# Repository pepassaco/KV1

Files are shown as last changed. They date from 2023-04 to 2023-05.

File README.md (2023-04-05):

# KV1: A hydrofoil-based flying kayak 

**IMPORTANT**: This project is currently UNDER DEVELOPMENT and in the prototyping stage. As a result, the final deisgn has not been tested yet. Build it at your own risk. Any kind of advice, testing or collaboration will be highly appreciated :)

## Recommended guides and related projects

First things first. 

- Optimal Cl/Cd ratio: [video](https://www.youtube.com/watch?v=RyCcKV8puSE)
- Calculating lift in hydrofoils: [Forum discussion](https://www.boatdesign.net/threads/calculating-lift-bernoulli-forces-on-hydrofoil-for-windsurfing-board.60062/)
- List of tutorials on how to design and simulate an airfoil(/hydrofoil) in XFLR 5 from zero (in Spanish): [link 1](https://www.youtube.com/watch?v=bGubYDDyFB4), [link 2](https://www.youtube.com/watch?v=IUO3XJQxrvs), [link 3](https://www.youtube.com/watch?v=fuJba9P9ncE), [link 4](https://www.youtube.com/watch?v=owMY_eJGt3o)
- What we want to achieve: [video 1](https://www.youtube.com/watch?v=-VyOZVtOWoI)

## Design considerations

The design stage of this project took place under the following constraints:

- At cruising speed, no part of the hull must be touching the water
- The foils must be able to lift a person with a body mass of at least 90Kg
- The hydrodynamic lift must be greater than the weight of the paddler and the vessel for velocities as low as 3.5m/s
- All of the above must take place in fresh calm water at at least 15ºC

While due to their fluid-mechanical nature these are the main considerations to have into account in this stage, there are other important conditions for this project to succeed, such as the hydrofoils being relatively lightweight and resilient or being able to manufacture with enough accuracy.

## Obtaining the right airfoil shape

The very first step in this case is analysing our fluid so that we can adequately choose the optimal hydrodynamic foil shape. Assuming an average salinity of our water of 10g/Kg, at 15ºC, its kinematic viscosity will be of about 1,15e6 m^2/s: 

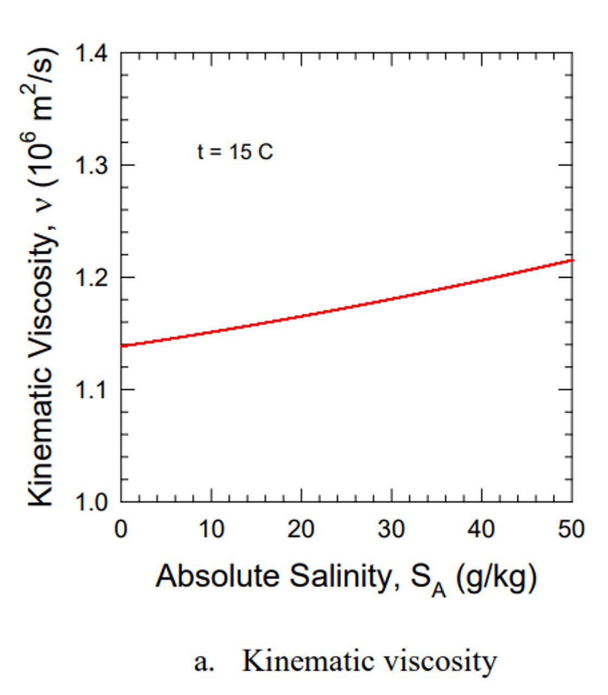
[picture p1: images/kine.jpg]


Pluggin this value in the definition of Reynold's NUmber, we get Re ~ 5.2e5:

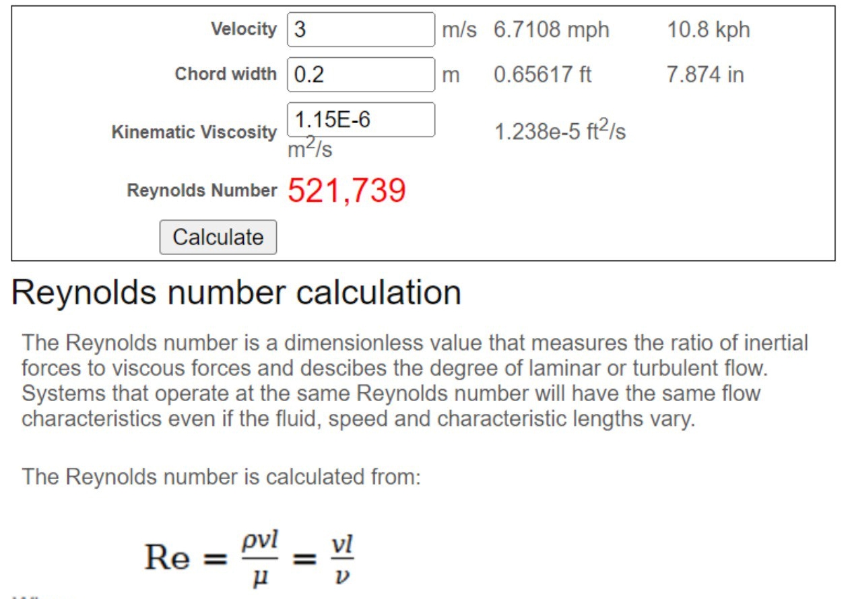
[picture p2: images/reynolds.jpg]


Taking this value into account, it was determined that an airfoil [NACA 4412](http://airfoiltools.com/airfoil/details?airfoil=naca4412-il) resulted in one of the best candidates to be used in this project, due to both its high lift coefficient (Cl) as well as lift-drag tadio (Cl/Cd) at low Angles of Attack:

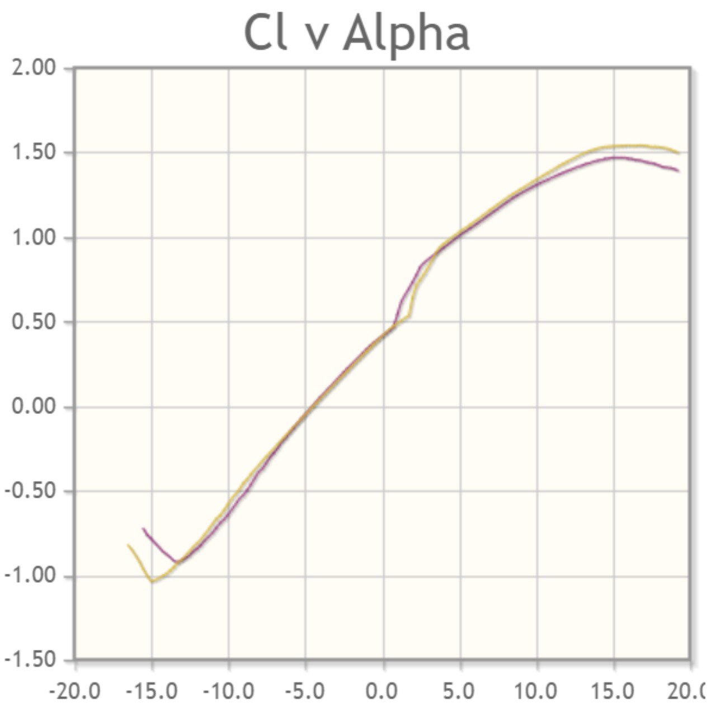
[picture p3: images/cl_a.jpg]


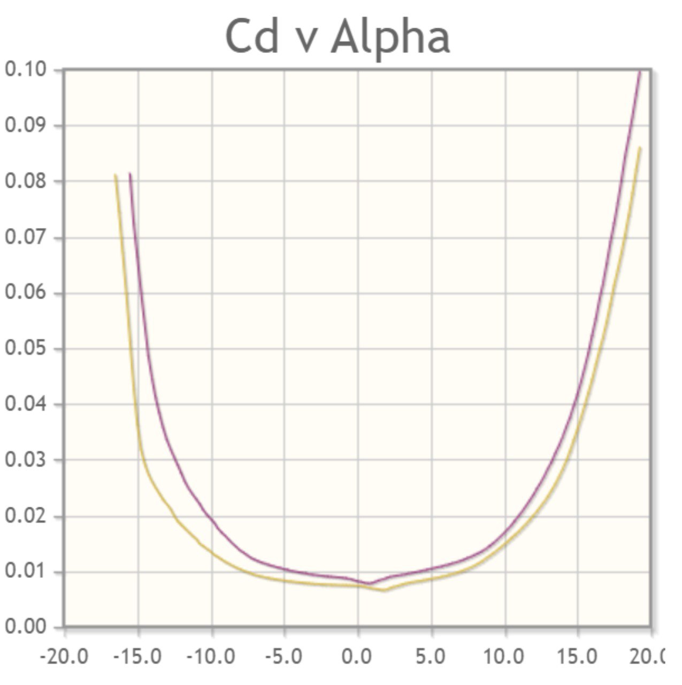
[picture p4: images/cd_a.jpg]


Moreover, it was decided that at cruising speed, the AoA of the main foil should be of 5º in order to maximize Cl/Cd. 

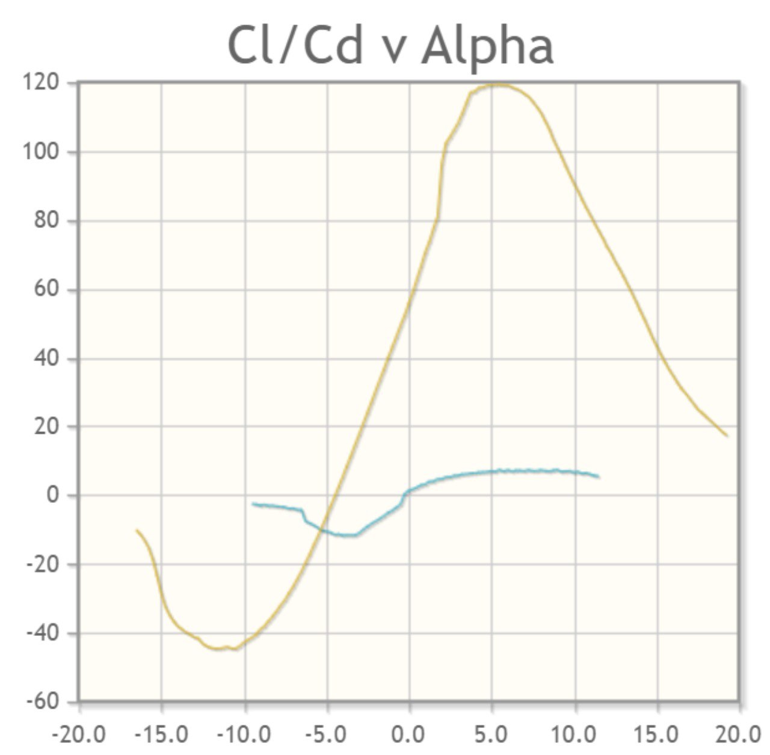
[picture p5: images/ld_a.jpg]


Note however that in the transition phase from water to air, we expect the front hydrofoil to lift first, inducing an extra AoA in the main wing. Taking into accoun the geometry of a K1 (5,4m of length), this increase in the AoA can be obtained in an approximate way (it will depend on the final position in the Z axis of the foils) achieving values from 5º to 8º, leading to global AoAs of between 10º and 13º. As we can see in the plot of Cl vs AoA, these are exactly the angles that maximize lift, helping pushing the paddler upwards.

## Computing the shape and angles of the hydrofoils

The shape and angles of the hydrofoils were obtained by means of the numerical simulation software [XFLR5](https://sourceforge.net/projects/xflr5/files/). First, an approximation for the global size of the airfoils was determined in terms of the lift force we require. Then, their aspect ratios were chosen so that they are the largest possible (for minimising drag) without impacting the maneuverability of the vessel (excessively long hydrofoils can be unconfortable for paddling) and manufacturing requirements (in our particular case, the longest piece must be less than 1m long). Finally, it was time to tweek the remaining parameters: the exact position of the hydrofoils in the X axis of the vessel with respect to the center of mass, their depth or position in the Z axis, the AoA of the front foil and the shape and width of the masts that will attach the foils to the hull.

The optimization of these parameters was carried out by finding a slightly positive Momentum Coefficient (Cm) at 0º of vessel pitching that becomes 0 for low pitching angles (around 2º in this case). The physical meaning of this is that, when reaching certain threshold speed (the rotation speed) with the kayak perfectly flat, the lift generated will be enought for both lifting the bow, generating pitching in the vessel and increasing the AoA. At 2º of pitching, Cm will equal 0, so it should remain in that orientation indefinitely:

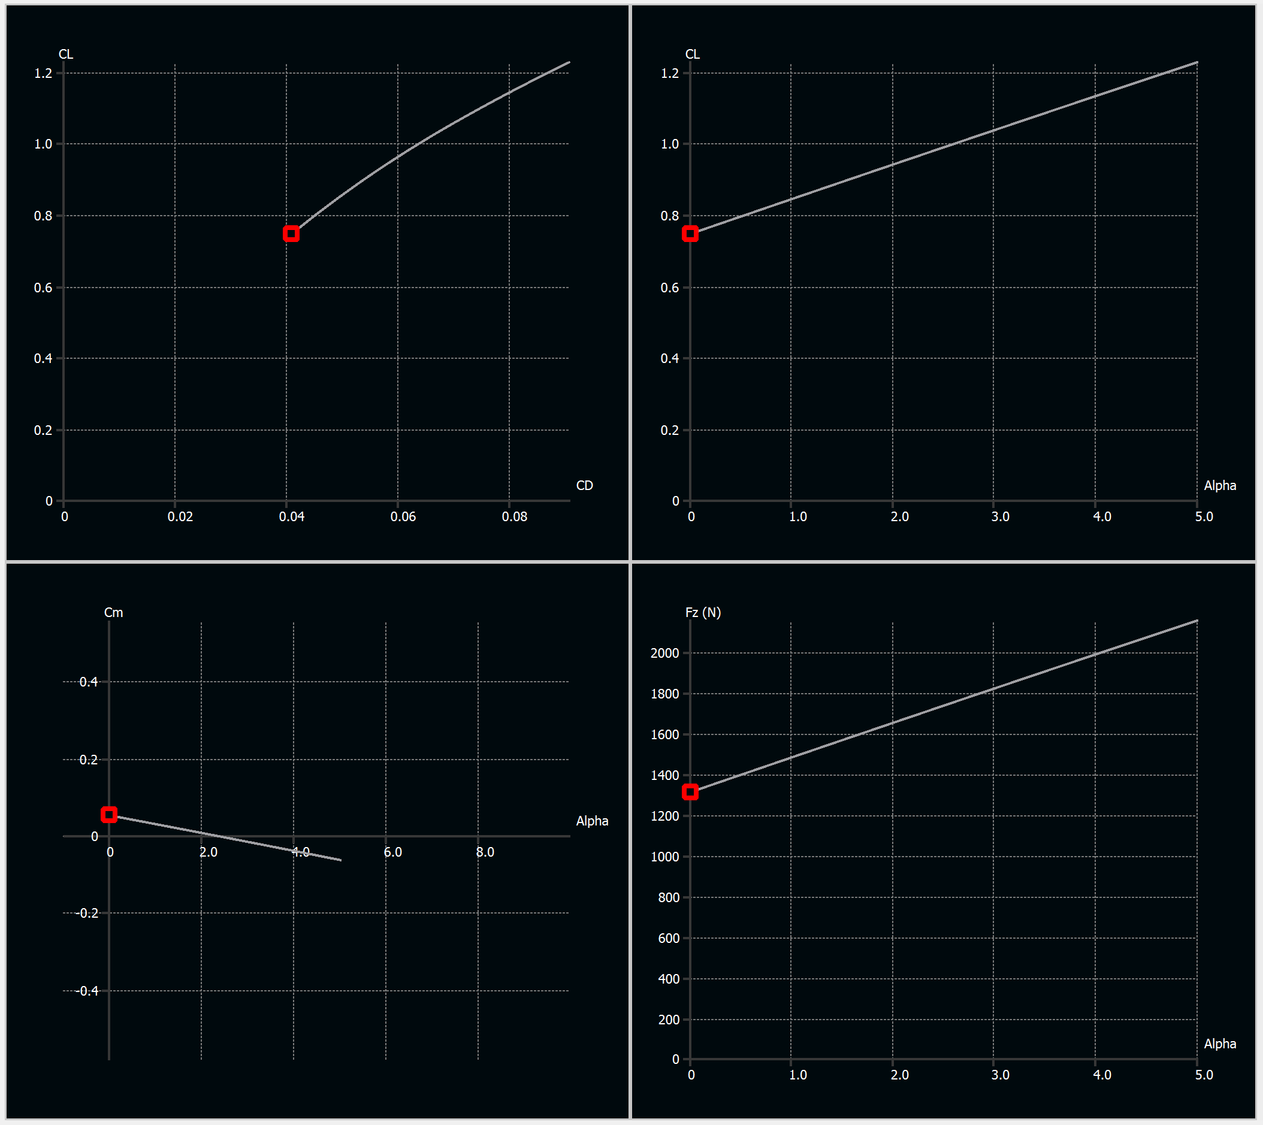
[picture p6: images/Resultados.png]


Note that, in the lower-right plot, we can see the lift force caused by both hydrofoils. It is always greater than 1200N, so that, even assuming a relatively large security margin, the lift forces will cancel out (and even be greater than) the weigth forces, so the vessel will start "flying".

The final deign can be seen in the following images (the XFLR5 file is also included in the folder simulations/):

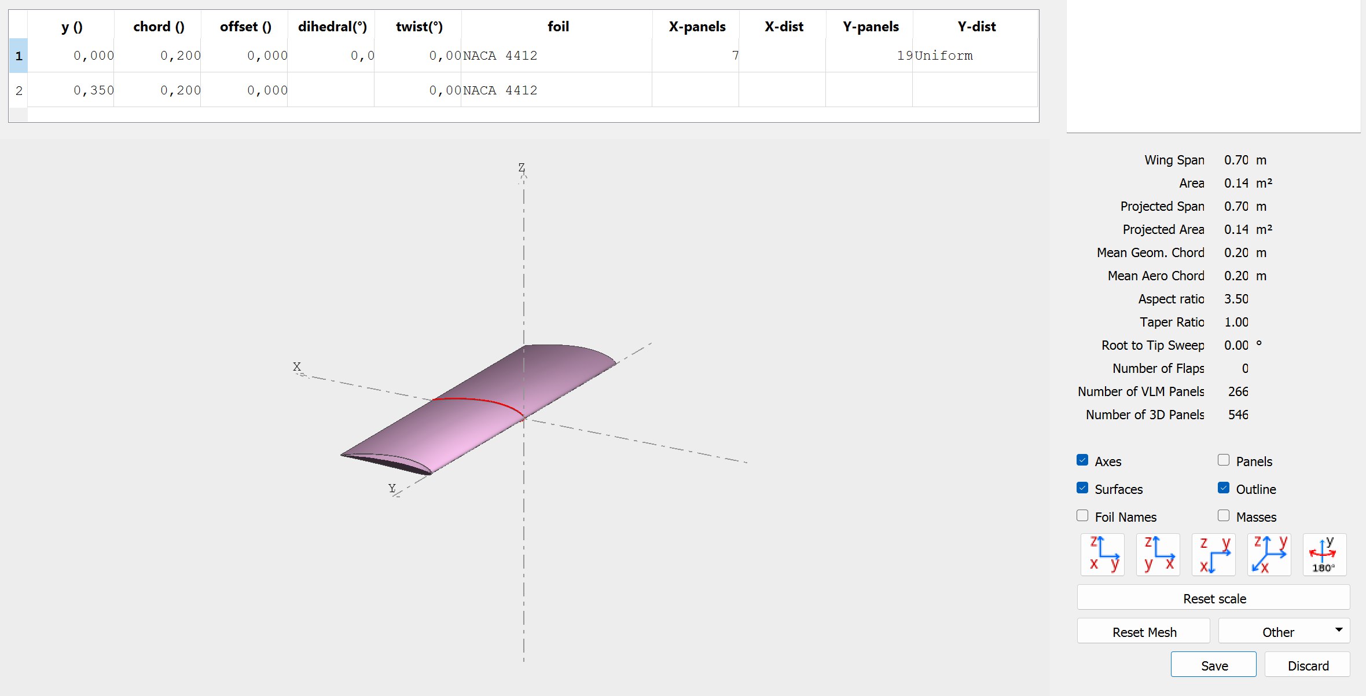
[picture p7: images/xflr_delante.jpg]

Front hydrofoil

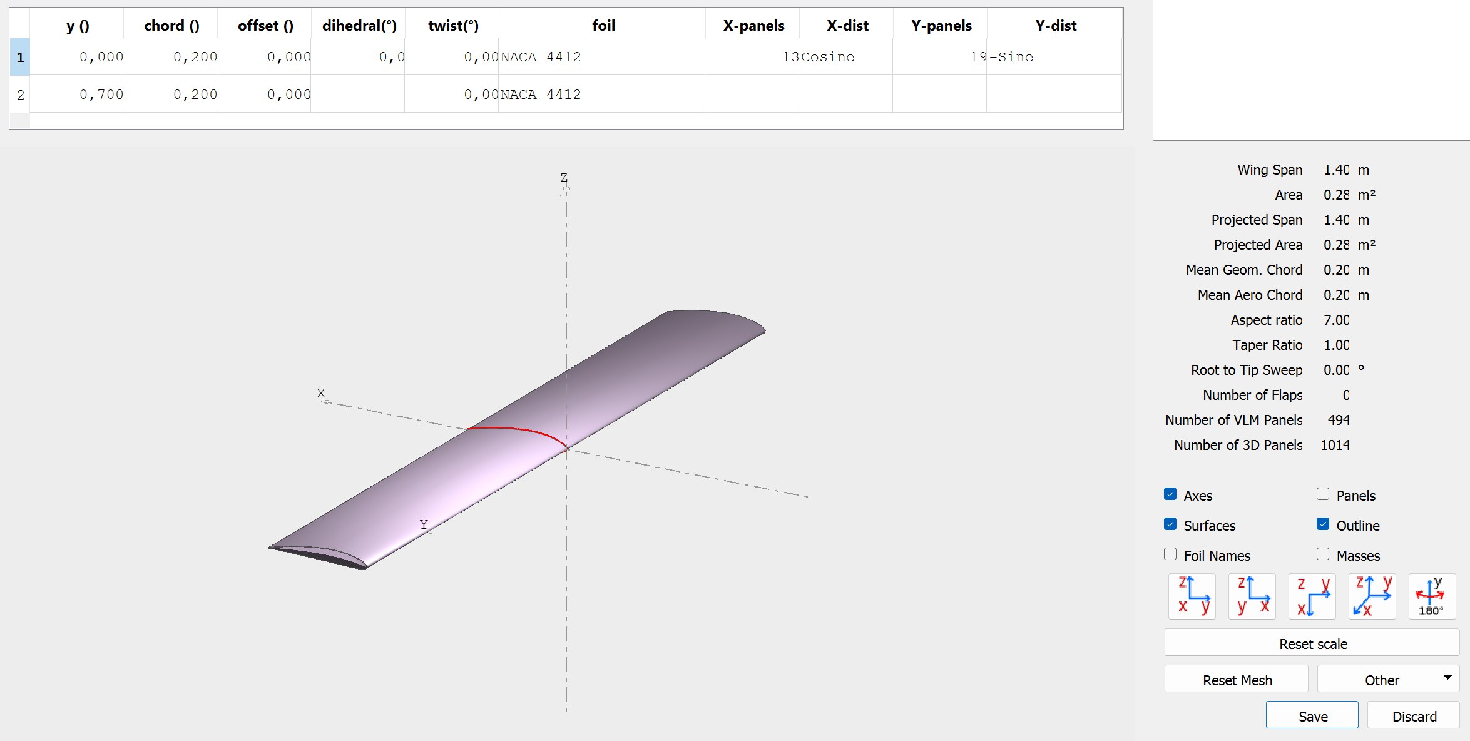
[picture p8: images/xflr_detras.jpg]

Rear hydrofoil

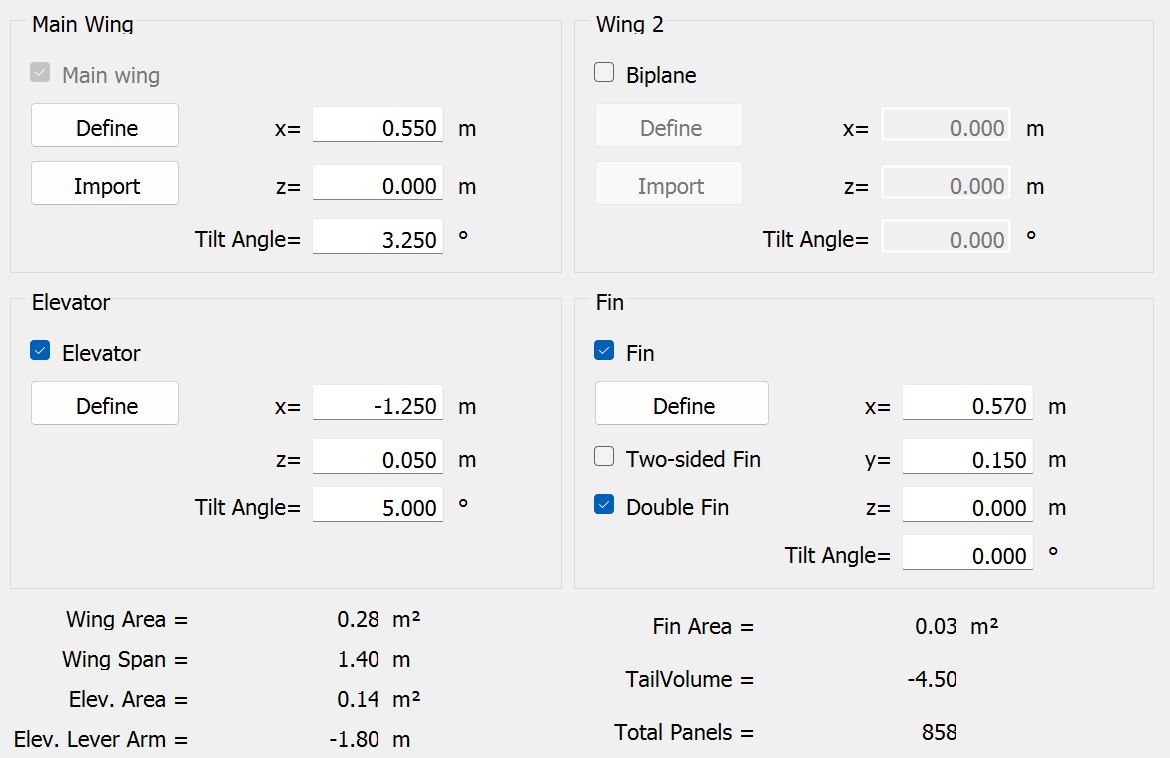
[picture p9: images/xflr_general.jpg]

General geometry

The airfoil chosen for the masts is a [NACA 0012](http://airfoiltools.com/airfoil/details?airfoil=n0012-il) due to its low drag properties:

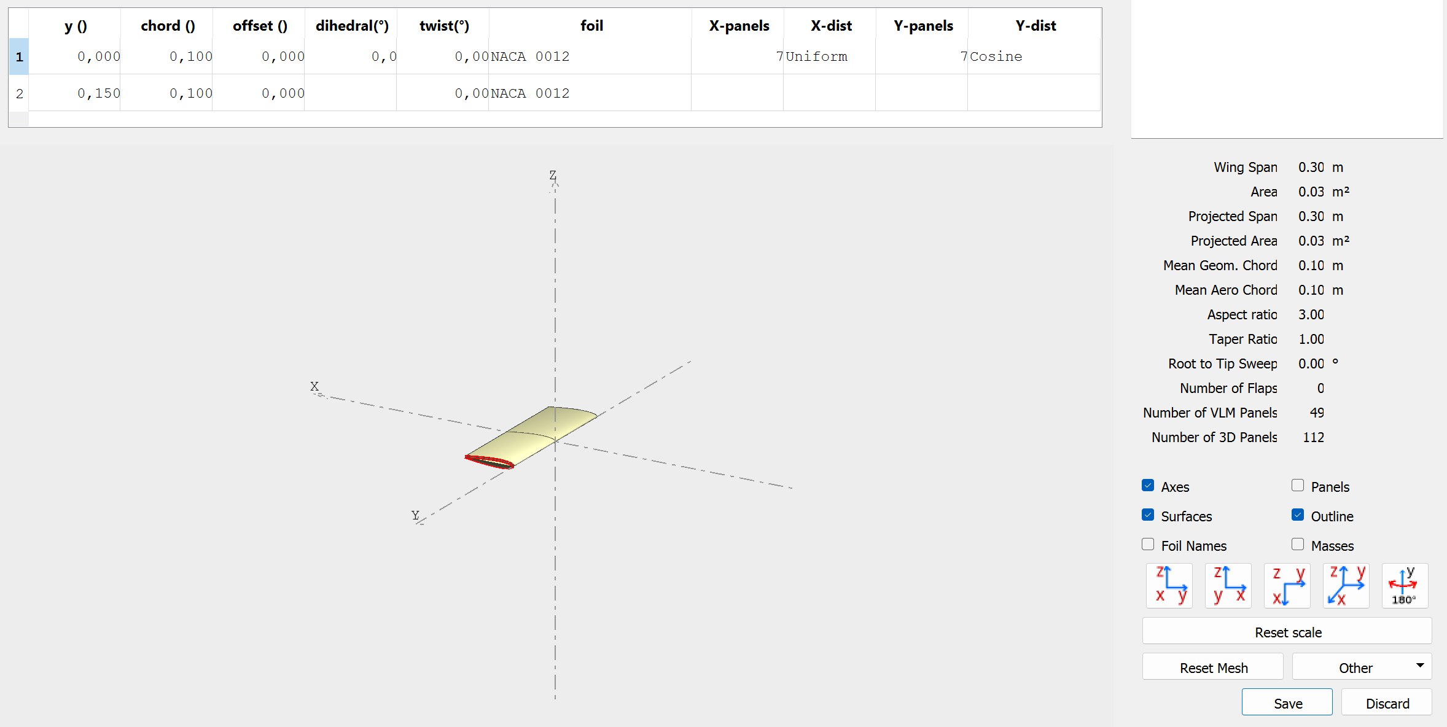
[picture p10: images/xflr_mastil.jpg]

NACA 0012 mast

And these are the final simulation results for a kayak velocity of 3,5m/s and no angle of attack:

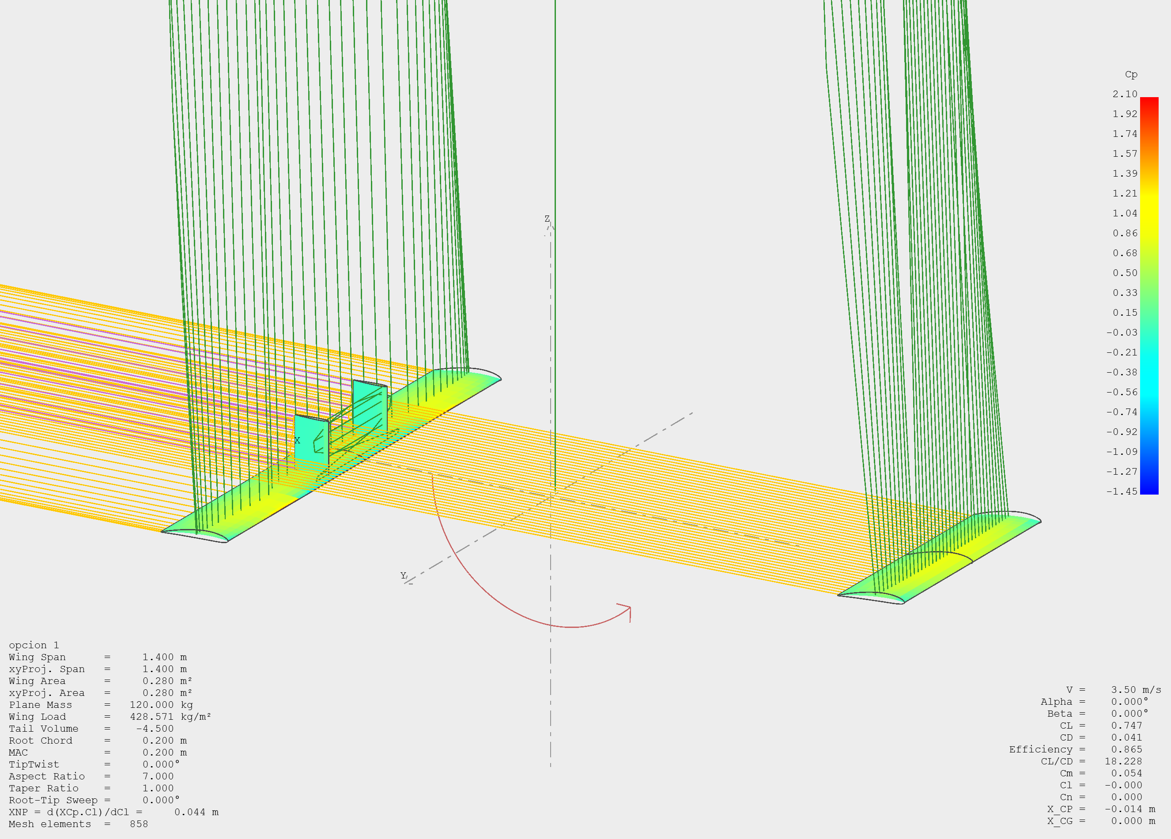
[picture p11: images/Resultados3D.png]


## Manufacturing and assembly

*Note:* this stage has not been finished yet.

Currently, the best approach we could ifnd for manufacturing these hydrofoils at home in a cheap and resilient way is by 3D printing. These parts will not be lightweight enough for a final build, but they can definitely serve a prototyping purpose. 

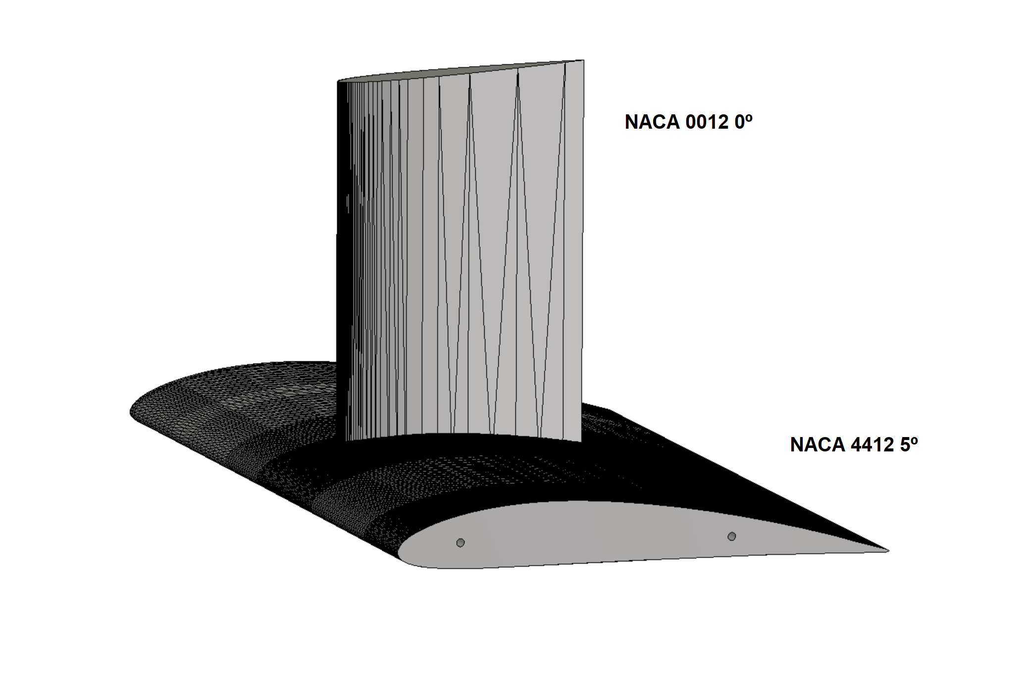
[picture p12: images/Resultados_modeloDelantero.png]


The rear hydrofoil was splitted into four different parts (one center part, two laterals and the mast) in order to fit in a common 3D printer. Holes for joining them through aluminum rods were also inserted in the design. You can find the STL files in the models/ folder.

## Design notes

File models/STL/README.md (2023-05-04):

These STL files are currently under testing. Use at your own risk!

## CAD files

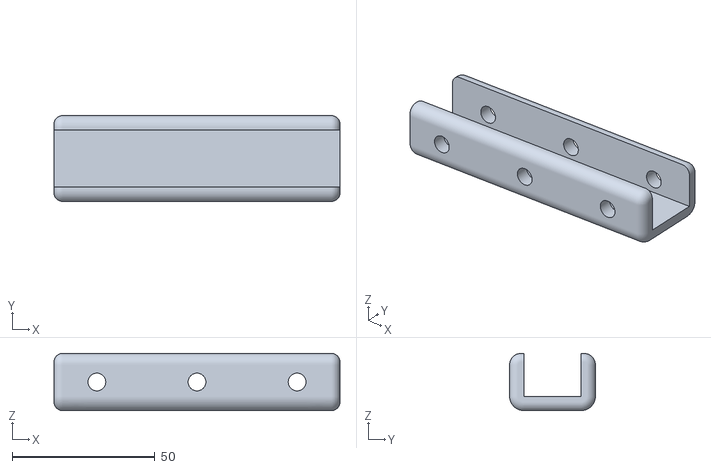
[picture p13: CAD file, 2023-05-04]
models/STL/Wing_hitch_(debugOnly).stl
100.0 x 30.0 x 20.0

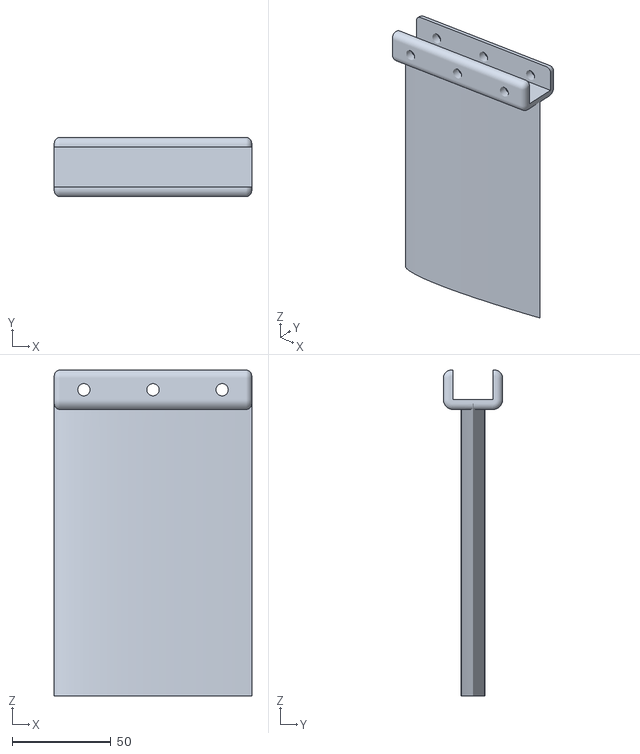
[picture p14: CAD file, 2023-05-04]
models/STL/Front_fin.stl
100.0 x 30.0 x 165.0

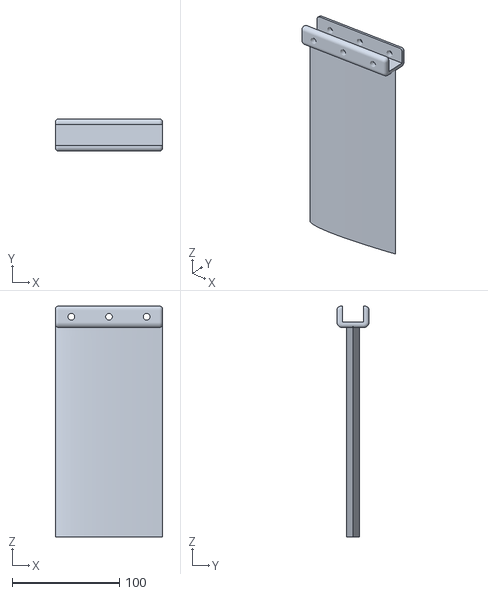
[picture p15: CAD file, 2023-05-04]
models/STL/Rear_fin.stl
100.0 x 30.0 x 215.0

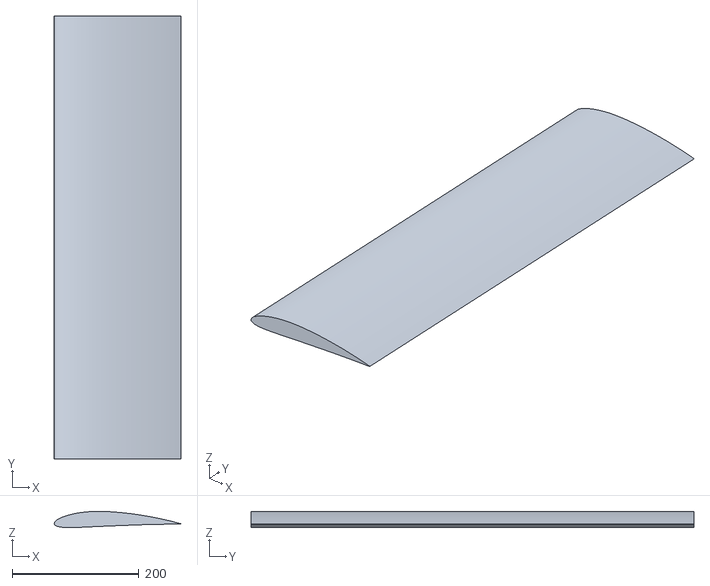
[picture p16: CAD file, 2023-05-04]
models/STL/Front_wing.stl
200.0 x 700.0 x 25.5

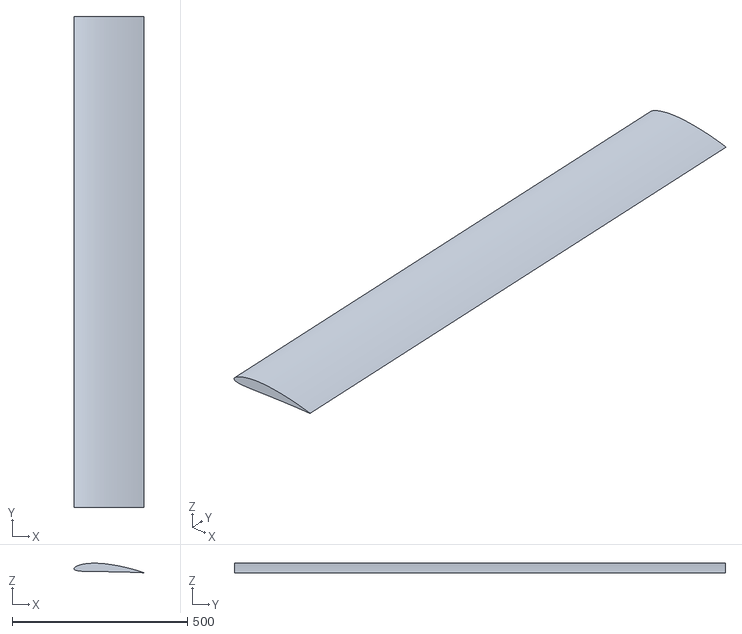
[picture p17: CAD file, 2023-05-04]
models/STL/Rear_wing.stl
199.7 x 1400.0 x 27.7

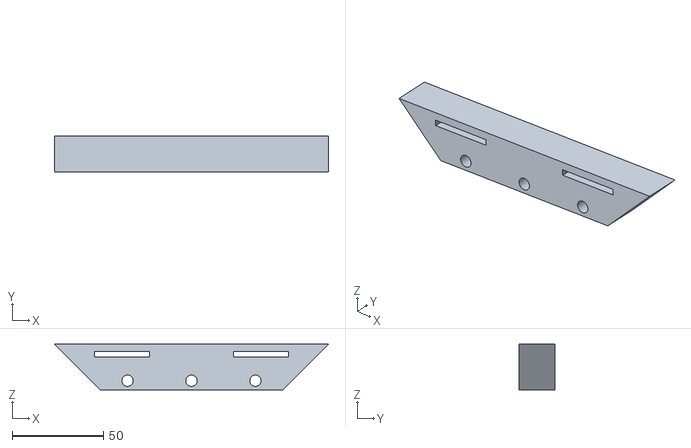
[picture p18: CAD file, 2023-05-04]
models/STL/Hull_hitch.stl
150.0 x 19.5 x 25.0
